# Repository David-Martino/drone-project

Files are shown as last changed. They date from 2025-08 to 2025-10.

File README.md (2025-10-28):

# ELEC5550 3D Mapping and Navigating Autonomous Drone
This is the repository for Team 0-05's final year design project for ELEC5550. The project is to build a drone system capable of autonomously mapping indoor spaces in 3D using onboard sensors, while meeting restrictive power and cost constraints (a 2S 800mAh battery and a $500 budget). Navigation is done using ROS2, running on a ground station connected to the drone over Wi-Fi. Mapping is also done on ROS2, based on UZ-SLAMLab's implementation of ORB-SLAM3 for Visual SLAM and Kimberly McGuire's crazyflie_ros2_multiranger repository for the ToF mapping. The flight controller is based on Espressif's ESP-Drone library, which itself is based on Bitcraze's Crazyflie flight kernel.

<center>

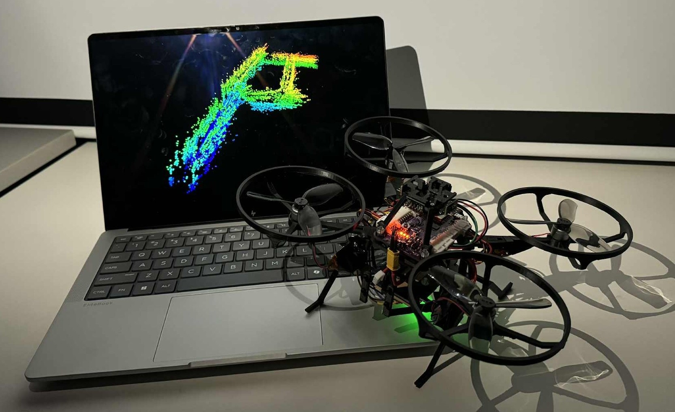
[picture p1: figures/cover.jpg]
Cover


</center>

# Key features 
- Visual SLAM 3D mapping using a monocular Raspberry Pi Camera 3
- Navigation and mapping using an omnidirectional VL53L1 ToF lidar array
- Onboard obstacle avoidance
- Automatic emergency landing procedure for communication loss or critically low battery events.
- Integration with ROS with the option for manual control

# Requirement Verification Evidence
### Test VSM-02: ORB-SLAM3 and Lidar Map
The maps are exported as OctoMap files (.bt). Examples can be found under the `Examples` folder.

ORB-SLAM3             |  ToF Array
:-------------------------:|:-------------------------:
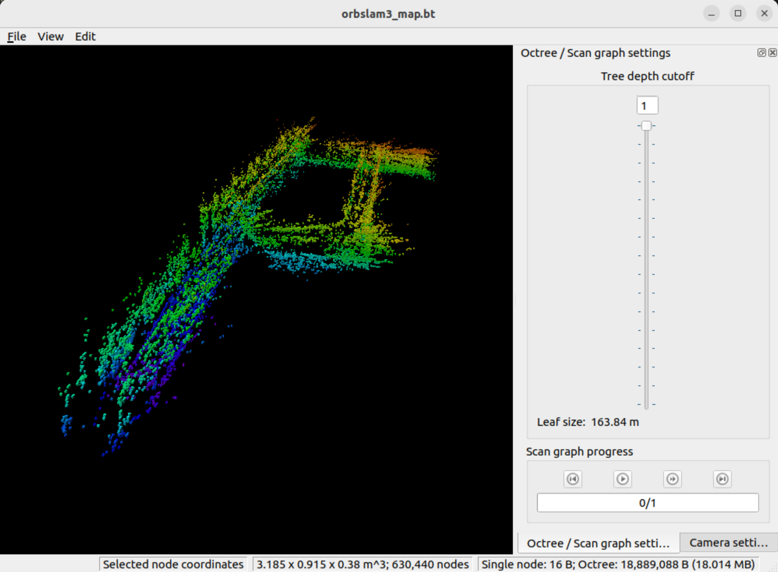
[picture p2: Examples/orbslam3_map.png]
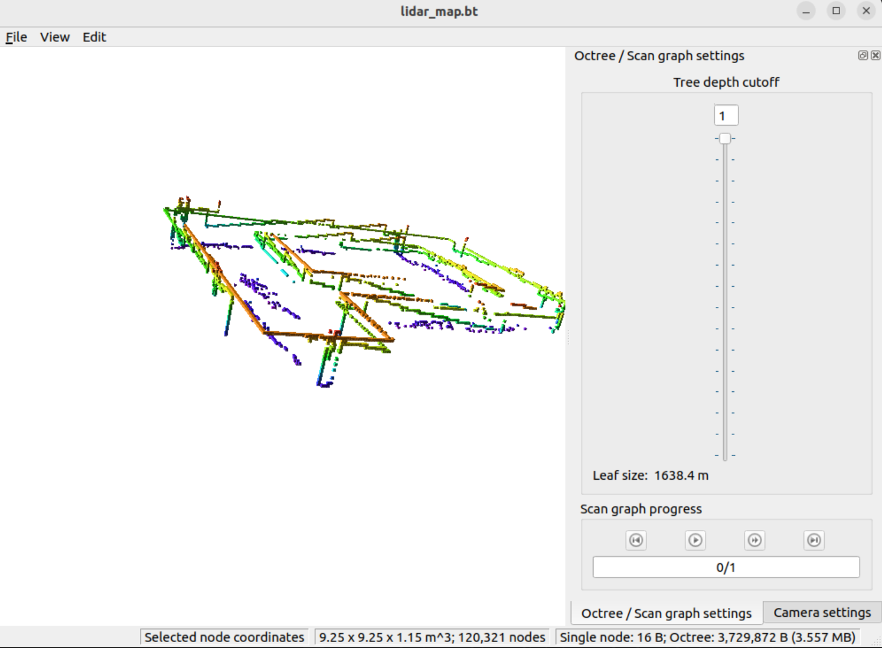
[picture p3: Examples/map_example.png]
  |  

### Test LDR-02: Real-time mapping using the ToF array

<center>

LDR-02 Verfication

</center>

### Test FC-04: Obstacle Avoidance
<center>

FC-04 Verfication

</center>

### Test FC-05: Communication Loss Emergency Landing
The critical battery event follows the same landing procedure, triggering 5 seconds after the event is detected.
<center>

FC-05 Verfication

</center>

# Issues
- Cheap 1104 BLDC motors overheating after ~40 seconds of flight time.
- Significant positional drift while publishing velocity commands.
- ORB-SLAM3 map is not scaled correctly.
- Optical Flow Deck could not be manufactured easily. A VL53L1 breakout board and a PMW3901 breakout board were used for the demonstration.

# Future Work
- Upgrading the FC MCU from an ESP32-S3 to an ESP32-P4. This MCU has hardware H.264 encoding, allowing us to remove the Raspberry Pi and hence vastly reduce the size and weight of the platform.
- Upgrading from visual SLAM to a visual-inertial SLAM using the IMU data for improved map accuracy.
- Changing frame to a more stiff carbon frame (the 3D printed ABS frame is quite flexible, although its unclear if the stability is actually affected by this)
- Custom BLDC ESCs mounted in a more secure location
- Frontier exploration scheme to deterministically map an entire space.
- Improve manufacturability of Optical Flow Deck by extending the pads of the PMW3901 and VL53L1 sensors out from beneath of the component.

# Licence
- Firmware: The firmware folder content is licensed under LGPL-3.0

- Software: The software folder content is released under GPLv3. The dependencies in this workspace are listed below. For a full list of the dependency's licenses, refer to their documentation.
    - ORB-SLAM3 (released under GPLv3)
    - Kimberley McGuire's lidar mapping project (released under the MIT License)

- Hardware: The hardware folder content is licensed under CC-BY-NC-SA 4.0

- Frame: The frame content is licensed under CC-BY-NC-SA 4.0

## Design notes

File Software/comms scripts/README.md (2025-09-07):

# Erwin's Attempt at Implementing David's Scripts

1. Install `Raspberry Pi Imager` on Windows (Ubuntu dual boot wasn't seeing the SD card).
1. Plug in micro SD card (in standard SD card adapter) with write lock off (if present).
1. Choose Device as `Raspberry Pi Zero 2 W`.
1. Choose OS as `Raspberry Pi OS Lite (64-bit)` under Raspberry Pi OS (Other).
1. Choose Storage as the micro SD card you plugged in.
1. Click Next and configure OS settings:
    1. Set username and password (`erwin`, `12345678`).
    1. Configure wireless LAN (`iPhone98`, `12345678`, `AU`).
    1. Set locale settings (`Australia/Perth`, `au`).
    1. Enable SSH (select `Use password authentification`).
1. Continue to flash the SD card.
1. On iPhone hotspot, turn on `Allow Others to Join` and `Maximise Compatibility` to force 2.4GHz wifi.
1. Plug micro SD card into Pi Zero 2 W and start up, with keyboard and monitor connected.
1. Once booted, log in with username and password. 
1. Wait a minute and check if connected to the hotspot with `nmcli device status` and `hostname -I`.
1. If not connected, configure wifi settings with:
    1. Confirm hotspot is visible with `nmcli dev wifi list`.
    1. Connect to hotspot with `sudo nmcli dev wifi connect "iPhone98" password "12345678" ifname wlan0`.
    1. Check connection is in list of saved connections with `nmcli con show`.
    1. Configure autoconnection with `sudo nmcli con mod "iPhone98" connection.autoconnect yes`.
    1. Reboot with `sudo reboot`.
    1. Wait a minute and check if connected to the hotspot with `nmcli device status` and `hostname -I`.
1. Connect to the hotspot with your groundstation.
1. Test SSH connection from your groundstation with `ssh erwin@raspberrypi.local` and `12345678`. 
1. Open a terminal on the groundstation, navigate to `drone-project\comms script\Beacon\`, and run `python .\gs_beacon.py`.
1. Install GStreamer from `https://gstreamer.freedesktop.org/download/#windows` (download and run `MSVC 64-bit runtime installer`).
1. Add GStreamer to path (`C:\Program Files\gstreamer\1.0\msvc_x86_64\bin` on Windows).
1. Launch GStreamer with `gst-launch-1.0 -v udpsrc port=5004 caps="application/x-rtp, media=video, encoding-name=H264, payload=96" ! rtph264depay ! h264parse ! avdec_h264 ! videoconvert ! autovideosink sync=false`. 
1. On the Pi (or via SSH), install with the following:
    ```
    sudo apt update
    sudo apt full-upgrade -y
    sudo reboot
    sudo apt -y install gstreamer1.0-tools gstreamer1.0-plugins-base gstreamer1.0-plugins-good gstreamer1.0-plugins-bad gstreamer1.0-plugins-ugly ffmpeg python3-pip rpicam-apps iperf3
    ```
1. On the groundstation, navigate to `drone-project\comms script\` and copy with the following:
    ```
    scp Beacon\discover_gs.py Startup\Pi-Startup-FFmpeg.service_RevC.service Vido_Uplink\ffmpeg_uplink_RevE.bash erwin@raspberrypi.local:/home/erwin/
    ```
1. On the Pi (or via SSH), move and rename files with the following:
    ```
    sudo mv ~/discover_gs.py /usr/local/bin/
    sudo mv ~/ffmpeg_uplink_RevE.bash /usr/local/bin/ffmpeg_uplink.sh
    sudo chmod +x /usr/local/bin/discover_gs.py /usr/local/bin/ffmpeg_uplink.sh
    sudo mv ~/Pi-Startup-FFmpeg.service_RevC.service /etc/systemd/system/pi-uplink.service
    sudo systemctl daemon-reload
    ```
1. On the Pi (or via SSH), use `sudo nano /etc/systemd/system/pi-uplink.service` to edit the User from `piteam05` to `root`, then save (CTRL+O, ENTER) and exit (CTRL+X).
1. Fix Windows line endings with:
    ```
    sudo apt -y install dos2unix
    sudo dos2unix /usr/local/bin/ffmpeg_uplink.sh /usr/local/bin/discover_gs.py /etc/systemd/system/pi-uplink.service
    ```
1. On the Pi (or via SSH), disable the Pi video preview with `sudo sed -i '0,/rpicam-vid /s//rpicam-vid -n /' /usr/local/bin/ffmpeg_uplink.sh`.  
1. On the Pi (or via SSH), set environment variables and launch streaming with `BASE_IP=172.20.10.6 PORT=5004 W=1280 H=720 FPS=30 BITRATE=4000000 GOP=15 ffmpeg_uplink.sh`. End with `CTRL+C`.
1. On the Pi (or via SSH), change the uplink service details with `sudo nano /etc/systemd/system/pi-uplink.service` to match the following:
    ```
    [Unit]
    Description=Pi Camera → RTP/UDP uplink (beacon + IP fallback)
    After=network-online.target
    Wants=network-online.target

    [Service]
    Type=simple
    User=root
    Group=video
    # Discovery config:
    Environment=BEACON_PORT=9000
    Environment=DISCOVERY_TIMEOUT=20
    Environment=SERVICE_NAME=GS-H264
    # Final fallback:
    Environment=BASE_IP=172.20.10.6
    # Video params:
    Environment=PORT=5004
    Environment=W=1280
    Environment=H=720
    Environment=FPS=30
    Environment=BITRATE=4000000
    Environment=GOP=15
    ExecStartPre=/bin/sleep 3
    ExecStart=/usr/local/bin/ffmpeg_uplink.sh
    Restart=always
    RestartSec=2

    [Install]
    WantedBy=multi-user.target
    ```
1. On the Pi (or via SSH), test the service with:
    ```
    sudo systemctl daemon-reload
    sudo systemctl start pi-uplink.service
    journalctl -u pi-uplink.service -n 20 --no-pager
    ```
1. On the Pi (or via SSH), stop the service and enable autostart with:
    ```
    sudo systemctl stop pi-uplink.service
    sudo systemctl enable --now pi-uplink.service
    ```
1. On the Linux groundstation, install with:
    ```
    sudo apt update && sudo apt -y install \
    gstreamer1.0-tools \
    gstreamer1.0-plugins-base \
    gstreamer1.0-plugins-good \
    gstreamer1.0-plugins-bad \
    gstreamer1.0-plugins-ugly \
    gstreamer1.0-libav \
    ffmpeg \
    python3 \
    python3-pip \
    iperf3
    ```
1. On the Linux groundstation, mnually test receiving the video stream with:
    ```
    gst-launch-1.0 -v udpsrc port=5004 \
    caps="application/x-rtp, media=video, encoding-name=H264, payload=96" \
    ! rtpjitterbuffer latency=60 \
    ! rtph264depay ! h264parse ! avdec_h264 ! videoconvert ! autovideosink sync=false
    ```

To start streaming:
1. Turn on hotspot with `Maximise Compatibility` on.
1. Connect to hotspot from groundstation.
1. CD to `drone-project` directory in terminal and run `make stream`.
1. Power up the Raspberry Pi Zero 2 W, and streaming should start within 30 seconds.

Run `make stop` to end streaming and beaconing on the groundstation.

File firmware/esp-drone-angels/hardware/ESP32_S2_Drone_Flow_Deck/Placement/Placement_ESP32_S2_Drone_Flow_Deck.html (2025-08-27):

D:\newFiles\e32336_esp32s2DroneShield\02_PCB\PCB_200616.pcb Create in 2020/6/16 20:44:25 Total components = 51 component(s)

Component Report
NO. | RefDes | PartDecal | Pins | Layer | Orient | PositionX | PositionY | IsSMD
1 | 1C1 | C0603 | 2 | Top | 180 | 13.100 | 38.379 | Yes
2 | 1C2 | C0402 | 2 | Top | 180 | 13.350 | 37.129 | Yes
3 | 1C3 | C0603 | 2 | Top | 180 | 13.050 | 35.879 | Yes
4 | 1C4 | C0402 | 2 | Top | 180 | 13.350 | 34.679 | Yes
5 | 1C5 | C0603 | 2 | Top | 180 | 13.100 | 32.629 | Yes
6 | 1C6 | C0402 | 2 | Top | 180 | 13.350 | 33.779 | Yes
7 | 1C7 | C0603 | 2 | Top | 0 | 13.100 | 45.879 | Yes
8 | 1C8 | C0603 | 2 | Top | 0 | 13.100 | 39.879 | Yes
9 | 1C9 | C0603 | 2 | Top | 0 | 18.300 | 46.979 | Yes
10 | 1C10 | C0402 | 2 | Top | 270 | 20.800 | 43.479 | Yes
11 | 1C11 | C0402 | 2 | Top | 0 | 18.050 | 45.729 | Yes
12 | 1J1 | CON8-S-2P0 | 16 | Bottom | 90 | 27.800 | 39.629 | No
13 | 1J2 | CON8-S-2P0 | 16 | Bottom | 90 | 2.800 | 39.629 | No
14 | 1R1 | R0402 | 2 | Top | 0 | 13.355 | 31.208 | Yes
15 | 1R2 | R0402 | 2 | Top | 180 | 7.300 | 32.629 | Yes
16 | 1R3 | R0402 | 2 | Top | 180 | 7.300 | 36.629 | Yes
17 | 1R4 | R0402 | 2 | Top | 180 | 7.300 | 38.629 | Yes
18 | 1R5 | R0402 | 2 | Top | 90 | 20.800 | 41.279 | Yes
19 | 1U1 | COB28_0P65_6X6 | 29 | Top | 0 | 18.300 | 34.629 | Yes
20 | 1U2 | SOT-23-5 | 5 | Top | 270 | 12.850 | 42.879 | Yes
21 | 1U3 | LGA12_0P8_2P5X4P9 | 12 | Top | 0 | 18.300 | 42.479 | Yes
22 | 2C1 | C0402 | 2 | Top | 180 | 8.050 | 12.016 | Yes
23 | 2C2 | C0402 | 2 | Top | 180 | 8.050 | 11.016 | Yes
24 | 2C3 | C0402 | 2 | Top | 90 | 11.800 | 14.766 | Yes
25 | 2C4 | C0402 | 2 | Top | 270 | 14.400 | 11.200 | Yes
26 | 2C5 | C0402 | 2 | Top | 270 | 13.400 | 11.200 | Yes
27 | 2C6 | C0402 | 2 | Top | 270 | 16.800 | 11.766 | Yes
28 | 2J1 | CON8-S-2P0 | 16 | Top | 90 | 2.800 | 11.766 | No
29 | 2J2 | CON8-S-2P0 | 16 | Top | 90 | 27.800 | 11.766 | No
30 | 2U1 | LPCC16_0P5_3X3 | 16 | Top | 0 | 11.050 | 11.766 | Yes
31 | 2U2 | QFN8_1P25_3X5 | 8 | Top | 0 | 19.550 | 11.766 | Yes
32 | T1 | HOLE_0P6 | 1 | Top | 0 | 7.000 | 27.864 | No
33 | T2 | HOLE_0P6 | 1 | Top | 0 | 7.900 | 27.864 | No
34 | T3 | HOLE_0P6 | 1 | Top | 0 | 8.800 | 27.864 | No
35 | T4 | HOLE_0P6 | 1 | Top | 0 | 9.700 | 27.864 | No
36 | T5 | HOLE_0P6 | 1 | Top | 0 | 10.600 | 27.864 | No
37 | T6 | HOLE_0P6 | 1 | Top | 0 | 10.600 | 23.500 | No
38 | T7 | HOLE_0P6 | 1 | Top | 0 | 9.700 | 23.500 | No
39 | T8 | HOLE_0P6 | 1 | Top | 0 | 8.800 | 23.500 | No
40 | T9 | HOLE_0P6 | 1 | Top | 0 | 7.900 | 23.500 | No
41 | T10 | HOLE_0P6 | 1 | Top | 0 | 7.000 | 23.500 | No
42 | T11 | HOLE_0P6 | 1 | Top | 0 | 19.600 | 27.864 | No
43 | T12 | HOLE_0P6 | 1 | Top | 0 | 20.500 | 27.864 | No
44 | T13 | HOLE_0P6 | 1 | Top | 0 | 21.400 | 27.864 | No
45 | T14 | HOLE_0P6 | 1 | Top | 0 | 22.300 | 27.864 | No
46 | T15 | HOLE_0P6 | 1 | Top | 0 | 23.200 | 27.864 | No
47 | T16 | HOLE_0P6 | 1 | Top | 0 | 19.600 | 23.500 | No
48 | T17 | HOLE_0P6 | 1 | Top | 0 | 20.500 | 23.500 | No
49 | T18 | HOLE_0P6 | 1 | Top | 0 | 21.400 | 23.500 | No
50 | T19 | HOLE_0P6 | 1 | Top | 0 | 22.300 | 23.500 | No
51 | T20 | HOLE_0P6 | 1 | Top | 0 | 23.200 | 23.500 | No

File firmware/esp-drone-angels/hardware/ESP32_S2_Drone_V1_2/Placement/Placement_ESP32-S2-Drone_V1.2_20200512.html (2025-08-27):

D:\WORK\#31436_ESP32-S2-ESPlane-KIT_M_V1.0_N_XX_20200325_V0.1\#31436_ESP32-S2-ESPlane-KIT_M_V1.2_N_XX_20200511_V0.3\02_PCB/PCB_ESP32-S2-Drone_V1.2_20200512.pcb Create in 2020/5/12 17:13:59 Total components = 203 component(s)

Component Report
NO. | RefDes | PartDecal | Pins | Layer | Orient | PositionX | PositionY | IsSMD
1 | C1 | C0603 | 2 | Top | 180 | 1571.554 | 2462.404 | Yes
2 | C2 | C0402 | 2 | Top | 90 | 1685.304 | 2562.104 | Yes
3 | C3 | C0603 | 2 | Top | 180 | 1555.454 | 2230.404 | Yes
4 | C4 | C0402 | 2 | Top | 270 | 1923.504 | 2559.904 | Yes
5 | C5 | C0402 | 2 | Top | 270 | 1771.004 | 2562.104 | Yes
6 | C6 | C0603 | 2 | Top | 0 | 2787.933 | 2016.722 | Yes
7 | C7 | C0402 | 2 | Top | 0 | 2808.406 | 1922.234 | Yes
8 | C8 | C0603 | 2 | Top | 180 | 2671.004 | 2016.722 | Yes
9 | C9 | C0402 | 2 | Top | 90 | 2750.925 | 1943.888 | Yes
10 | C10 | C0603 | 2 | Top | 180 | 1711.454 | 2230.404 | Yes
11 | C11 | C0603 | 2 | Top | 180 | 1706.504 | 2462.404 | Yes
12 | C12 | C0603 | 2 | Top | 180 | 1426.004 | 2117.254 | Yes
13 | C13 | C0402 | 2 | Top | 0 | 2231.004 | 2304.754 | Yes
14 | C14 | C0603 | 2 | Top | 90 | 2369.754 | 2361.004 | Yes
15 | C15 | C0603 | 2 | Top | 90 | 2169.754 | 2403.504 | Yes
16 | C16 | C0603 | 2 | Top | 180 | 2409.843 | 1237.402 | Yes
17 | C17 | C0402 | 2 | Top | 180 | 2398.031 | 1188.189 | Yes
18 | C18 | C0402 | 2 | Top | 270 | 1571.260 | 1214.173 | Yes
19 | C19 | C0402 | 2 | Top | 270 | 1852.254 | 2286.004 | Yes
20 | C20 | C0402 | 2 | Top | 0 | 2028.839 | 2377.254 | Yes
21 | C21 | C0402 | 2 | Top | 90 | 1959.604 | 2393.504 | Yes
22 | C22 | C0402 | 2 | Top | 180 | 1918.504 | 2141.004 | Yes
23 | C23 | C0402 | 2 | Top | 0 | 1139.370 | 1915.354 | Yes
24 | C24 | C0402 | 2 | Top | 0 | 1139.754 | 1604.754 | Yes
25 | D1 | SOD523 | 2 | Top | 315 | 1382.254 | 1399.754 | Yes
26 | D2 | SOD523 | 2 | Top | 45 | 1389.754 | 2547.254 | Yes
27 | D3 | SOD323 | 2 | Top | 90 | 2376.004 | 2237.254 | Yes
28 | D4 | SOD523 | 2 | Top | 135 | 2549.754 | 2552.254 | Yes
29 | D5 | SOD523 | 2 | Top | 0 | 2744.754 | 1419.754 | Yes
30 | D6 | LED3010-S | 3 | Top | 0 | 1476.378 | 2814.961 | Yes
31 | D7 | LED3010-S | 3 | Top | 180 | 1476.378 | 1122.047 | Yes
32 | D8 | LED3010-S | 3 | Top | 0 | 2460.630 | 2814.961 | Yes
33 | D9 | LED3010-S | 3 | Top | 180 | 2460.630 | 1122.047 | Yes
34 | FB1 | L0603 | 2 | Top | 90 | 2409.754 | 1328.504 | Yes
35 | H1 | P_2X1 | 1 | Bottom | 135 | 2814.964 | 2657.484 | Yes
36 | H58 | P_2X1 | 1 | Bottom | 45 | 708.661 | 3346.457 | Yes
37 | H59 | P_2X1 | 1 | Bottom | 45 | 1279.528 | 2814.961 | Yes
38 | H60 | P_2X1 | 1 | Bottom | 45 | 2657.480 | 1122.047 | Yes
39 | H61 | P_2X1 | 1 | Bottom | 45 | 3228.346 | 590.551 | Yes
40 | H62 | P_2X1 | 1 | Bottom | 135 | 1122.047 | 1279.528 | Yes
41 | H63 | P_2X1 | 1 | Bottom | 45 | 1122.047 | 2657.480 | Yes
42 | H65 | P_2X1 | 1 | Bottom | 45 | 3346.457 | 708.661 | Yes
43 | H66 | P_2X1 | 1 | Bottom | 135 | 2657.480 | 2814.961 | Yes
44 | H67 | P_2X1 | 1 | Bottom | 135 | 1279.528 | 1122.047 | Yes
45 | H68 | P_2X1 | 1 | Bottom | 135 | 590.551 | 708.661 | Yes
46 | H69 | P_2X1 | 1 | Bottom | 45 | 590.551 | 3228.346 | Yes
47 | H70 | P_2X1 | 1 | Bottom | 45 | 2814.961 | 1279.528 | Yes
48 | H71 | P_2X1 | 1 | Bottom | 135 | 3346.457 | 3228.346 | Yes
49 | H72 | P_2X1 | 1 | Bottom | 135 | 708.661 | 590.551 | Yes
50 | H73 | P_2X1 | 1 | Bottom | 135 | 3228.346 | 3346.457 | Yes
51 | J1 | USB_5P_MICRO_F | 11 | Top | 180 | 2638.504 | 2303.504 | No
52 | J2 | FFC24-0P5 | 26 | Top | 180 | 1968.504 | 2736.220 | Yes
53 | J3 | A2005HWV-S-XP-A | 16 | Top | 270 | 2460.630 | 1751.969 | No
54 | J4 | A2005HWV-S-XP-A | 16 | Top | 270 | 1476.378 | 1751.969 | No
55 | J5 | CON2X1_1P5_SMT_ZH-2A_DIP | 4 | Top | 45 | 2678.504 | 2678.504 | No
56 | J6 | CON2X1_1P5_SMT_ZH-2A_DIP | 4 | Top | 315 | 2678.504 | 1258.504 | No
57 | J7 | CON2X1_2P0_SMT_PH2A-S-A | 4 | Top | 270 | 1478.346 | 2288.504 | Yes
58 | J8 | CON2X1_1P5_SMT_ZH-2A_DIP | 4 | Top | 225 | 1258.504 | 1258.504 | No
59 | J9 | CON2X1_1P5_SMT_ZH-2A_DIP | 4 | Top | 135 | 1258.504 | 2678.504 | No
60 | J10 | A2005HWV-S-XP-A | 16 | Top | 270 | 1476.378 | 463.219 | No
61 | J11 | A2005HWV-S-XP-A | 16 | Top | 270 | 2460.630 | 463.219 | No
62 | Q3 | SOT-23-3 | 3 | Top | 180 | 1291.334 | 2033.504 | Yes
63 | Q4 | SOT-23-3 | 3 | Top | 0 | 1218.504 | 1512.004 | Yes
64 | Q5 | SOT-23-3 | 3 | Top | 270 | 1518.504 | 2667.254 | Yes
65 | Q6 | SOT-23-3 | 3 | Top | 90 | 2418.504 | 2667.504 | Yes
66 | Q7 | SOT-23-3 | 3 | Top | 0 | 2718.504 | 1512.004 | Yes
67 | R1 | R0402 | 2 | Top | 180 | 2533.504 | 2143.504 | Yes
68 | R3 | R0402 | 2 | Top | 0 | 2454.754 | 2143.504 | Yes
69 | R5 | R0402 | 2 | Top | 90 | 1868.404 | 2559.904 | Yes
70 | R6 | R0402 | 2 | Top | 270 | 1736.904 | 2562.104 | Yes
71 | R7 | R0402 | 2 | Top | 90 | 2709.193 | 1943.888 | Yes
72 | R8 | R0402 | 2 | Top | 0 | 2808.012 | 1963.967 | Yes
73 | R9 | R0402 | 2 | Top | 0 | 2646.201 | 1929.321 | Yes
74 | R10 | R0402 | 2 | Top | 0 | 2646.201 | 1964.754 | Yes
75 | R11 | R0402 | 2 | Top | 90 | 1321.260 | 1581.890 | Yes
76 | R12 | R0402 | 2 | Top | 90 | 1356.693 | 1581.890 | Yes
77 | R13 | R0402 | 2 | Top | 180 | 1232.254 | 1604.754 | Yes
78 | R14 | R0402 | 2 | Top | 180 | 1675.504 | 2619.904 | Yes
79 | R15 | R0402 | 2 | Top | 90 | 2583.996 | 1996.348 | Yes
80 | R16 | R0402 | 2 | Top | 270 | 2583.996 | 1916.148 | Yes
81 | R17 | R0402 | 2 | Top | 0 | 1253.504 | 2123.504 | Yes
82 | R18 | R0402 | 2 | Top | 180 | 2231.004 | 2267.854 | Yes
83 | R19 | R0402 | 2 | Top | 0 | 1139.754 | 1871.004 | Yes
84 | R20 | R0402 | 2 | Top | 90 | 2287.254 | 2288.504 | Yes
85 | R21 | R0402 | 2 | Top | 180 | 1538.976 | 1357.480 | Yes
86 | R22 | R0402 | 2 | Top | 90 | 1536.614 | 1214.173 | Yes
87 | R23 | R0402 | 2 | Top | 180 | 2381.004 | 2563.504 | Yes
88 | R24 | R0402 | 2 | Top | 90 | 2622.254 | 1529.754 | Yes
89 | R25 | R0402 | 2 | Top | 180 | 1538.976 | 1397.638 | Yes
90 | R26 | R0402 | 2 | Top | 180 | 1516.004 | 2763.504 | Yes
91 | R27 | R0402 | 2 | Top | 0 | 2018.604 | 2121.004 | Yes
92 | R28 | R0402 | 2 | Top | 0 | 1887.254 | 2377.254 | Yes
93 | R29 | R0402 | 2 | Top | 90 | 1448.504 | 1214.754 | Yes
94 | R30 | R0402 | 2 | Top | 180 | 2499.754 | 2763.504 | Yes
95 | R31 | R0402 | 2 | Top | 0 | 2476.772 | 1188.189 | Yes
96 | R32 | R0402 | 2 | Top | 270 | 2086.004 | 2360.504 | Yes
97 | R33 | R0402 | 2 | Top | 90 | 2086.004 | 2280.504 | Yes
98 | R34 | R0402 | 2 | Top | 0 | 1282.254 | 1759.754 | Yes
99 | R35 | R0402 | 2 | Top | 90 | 1344.754 | 1702.254 | Yes
100 | SW1 | SW4_3X3P5X1P1_SMT | 6 | Top | 270 | 1141.704 | 2047.244 | No
101 | SW2 | SW4_3X3P5X1P1_SMT | 6 | Top | 270 | 1141.732 | 1740.157 | No
102 | T1 | K_3X2 | 1 | Top | 0 | 68.504 | 2242.504 | No
103 | T2 | K_3X2 | 1 | Top | 0 | 68.504 | 2095.504 | No
104 | T3 | K_3X2 | 1 | Top | 0 | 720.472 | 2242.504 | No
105 | T4 | K_3X2 | 1 | Top | 0 | 720.472 | 2095.504 | No
106 | T5 | K_3X2 | 1 | Top | 0 | 68.504 | 1841.504 | No
107 | T6 | K_3X2 | 1 | Top | 0 | 68.504 | 1694.504 | No
108 | T7 | K_3X2 | 1 | Top | 0 | 720.474 | 1841.504 | No
109 | T8 | K_3X2 | 1 | Top | 0 | 720.472 | 1694.504 | No
110 | T9 | K_3X2 | 1 | Top | 180 | 1648.504 | 3512.254 | No
111 | T10 | K_3X2 | 1 | Top | 180 | 1648.504 | 3366.004 | No
112 | T11 | K_3X2 | 1 | Top | 180 | 3868.504 | 2242.504 | No
113 | T12 | K_3X2 | 1 | Top | 180 | 3868.504 | 2094.754 | No
114 | T13 | K_3X2 | 1 | Top | 180 | 2276.504 | 3512.254 | No
115 | T14 | K_3X2 | 1 | Top | 180 | 2276.504 | 3366.004 | No
116 | T15 | K_3X2 | 1 | Top | 180 | 3868.504 | 1841.504 | No
117 | T16 | K_3X2 | 1 | Top | 180 | 3868.504 | 1694.754 | No
118 | T17 | K_3X2 | 1 | Top | 0 | 3216.504 | 2242.504 | No
119 | T18 | K_3X2 | 1 | Top | 0 | 3216.504 | 2095.504 | No
120 | T19 | K_3X2 | 1 | Top | 0 | 3216.504 | 1841.504 | No
121 | T20 | K_3X2 | 1 | Top | 0 | 3216.504 | 1694.504 | No
122 | T21 | SMD_3X6 | 1 | Top | 225 | 3359.055 | 495.669 | No
123 | T22 | HOLE_0P6 | 1 | Top | 0 | 717.649 | 2527.559 | No
124 | T23 | SMD_3X6 | 1 | Top | 45 | 3881.102 | 136.220 | No
125 | T24 | SMD_3X6 | 1 | Top | 135 | 3813.386 | 3888.583 | No
126 | T25 | SMD_3X6 | 1 | Top | 315 | 3446.063 | 3375.591 | No
127 | T26 | SMD_3X6 | 1 | Top | 225 | 47.638 | 3812.205 | No
128 | T27 | SMD_3X6 | 1 | Top | 45 | 585.039 | 3433.071 | No
129 | T28 | SMD_3X6 | 1 | Top | 135 | 497.638 | 582.677 | No
130 | T29 | SMD_3X6 | 1 | Top | 315 | 124.409 | 45.669 | No
131 | T30 | HOLE_0P6 | 1 | Top | 0 | 717.649 | 2500.000 | No
132 | T31 | HOLE_0P6 | 1 | Top | 0 | 717.649 | 2472.441 | No
133 | T32 | HOLE_0P6 | 1 | Top | 0 | 717.649 | 2417.323 | No
134 | T33 | HOLE_0P6 | 1 | Top | 0 | 717.649 | 1519.685 | No
135 | T34 | HOLE_0P6 | 1 | Top | 0 | 717.649 | 1492.126 | No
136 | T35 | HOLE_0P6 | 1 | Top | 0 | 717.649 | 1464.567 | No
137 | T36 | HOLE_0P6 | 1 | Top | 0 | 717.649 | 1409.449 | No
138 | T37 | HOLE_0P6 | 1 | Top | 0 | 717.649 | 1437.008 | No
139 | T38 | HOLE_0P6 | 1 | Top | 0 | 1076.772 | 1519.685 | No
140 | T39 | HOLE_0P6 | 1 | Top | 0 | 1076.772 | 1492.126 | No
141 | T40 | HOLE_0P6 | 1 | Top | 0 | 1076.772 | 1464.567 | No
142 | T41 | HOLE_0P6 | 1 | Top | 0 | 1076.772 | 1409.449 | No
143 | T42 | HOLE_0P6 | 1 | Top | 0 | 1076.772 | 1437.008 | No
144 | T43 | HOLE_0P6 | 1 | Top | 0 | 1076.772 | 2531.496 | No
145 | T44 | HOLE_0P6 | 1 | Top | 0 | 1076.772 | 2503.937 | No
146 | T45 | HOLE_0P6 | 1 | Top | 0 | 1076.772 | 2476.378 | No
147 | T46 | HOLE_0P6 | 1 | Top | 0 | 1076.772 | 2448.819 | No
148 | T47 | HOLE_0P6 | 1 | Top | 0 | 1076.772 | 2421.260 | No
149 | T48 | HOLE_0P6 | 1 | Top | 0 | 3219.359 | 2531.496 | No
150 | T49 | HOLE_0P6 | 1 | Top | 0 | 3219.359 | 2503.937 | No
151 | T50 | HOLE_0P6 | 1 | Top | 0 | 3219.359 | 2476.378 | No
152 | T51 | HOLE_0P6 | 1 | Top | 0 | 3219.359 | 2448.819 | No
153 | T52 | HOLE_0P6 | 1 | Top | 0 | 3219.359 | 2421.260 | No
154 | T53 | HOLE_0P6 | 1 | Top | 0 | 3219.359 | 1515.748 | No
155 | T54 | HOLE_0P6 | 1 | Top | 0 | 3219.359 | 1488.189 | No
156 | T55 | HOLE_0P6 | 1 | Top | 0 | 3219.359 | 1460.630 | No
157 | T56 | HOLE_0P6 | 1 | Top | 0 | 3219.359 | 1433.071 | No
158 | T57 | HOLE_0P6 | 1 | Top | 0 | 3219.359 | 1405.512 | No
159 | T58 | HOLE_0P6 | 1 | Top | 0 | 717.649 | 2444.882 | No
160 | T59 | HOLE_0P6 | 1 | Top | 0 | 2860.236 | 1519.685 | No
161 | T60 | HOLE_0P6 | 1 | Top | 0 | 2860.236 | 1492.126 | No
162 | T61 | HOLE_0P6 | 1 | Top | 0 | 2860.236 | 1464.567 | No
163 | T62 | HOLE_0P6 | 1 | Top | 0 | 2860.236 | 1437.008 | No
164 | T63 | HOLE_0P6 | 1 | Top | 0 | 2860.236 | 1409.449 | No
165 | T64 | HOLE_0P6 | 1 | Top | 0 | 2860.236 | 2531.496 | No
166 | T65 | HOLE_0P6 | 1 | Top | 0 | 2860.236 | 2503.937 | No
167 | T66 | HOLE_0P6 | 1 | Top | 0 | 2860.236 | 2476.378 | No
168 | T67 | HOLE_0P6 | 1 | Top | 0 | 2860.236 | 2448.819 | No
169 | T68 | HOLE_0P6 | 1 | Top | 0 | 2860.236 | 2421.260 | No
170 | T69 | HOLE_0P6 | 1 | Top | 0 | 1549.291 | 1074.803 | No
171 | T70 | HOLE_0P6 | 1 | Top | 0 | 1576.850 | 1074.803 | No
172 | T71 | HOLE_0P6 | 1 | Top | 0 | 1604.409 | 1074.803 | No
173 | T72 | HOLE_0P6 | 1 | Top | 0 | 1631.969 | 1074.803 | No
174 | T73 | HOLE_0P6 | 1 | Top | 0 | 1549.291 | 925.197 | No
175 | T74 | HOLE_0P6 | 1 | Top | 0 | 1576.850 | 925.197 | No
176 | T75 | HOLE_0P6 | 1 | Top | 0 | 1604.409 | 925.197 | No
177 | T76 | HOLE_0P6 | 1 | Top | 0 | 1631.969 | 925.197 | No
178 | T77 | HOLE_0P6 | 1 | Top | 0 | 2305.315 | 925.197 | No
179 | T78 | HOLE_0P6 | 1 | Top | 0 | 2332.874 | 925.197 | No
180 | T79 | HOLE_0P6 | 1 | Top | 0 | 2360.433 | 925.197 | No
181 | T80 | HOLE_0P6 | 1 | Top | 0 | 2387.992 | 925.197 | No
182 | T81 | HOLE_0P6 | 1 | Top | 0 | 2305.315 | 1074.803 | No
183 | T82 | HOLE_0P6 | 1 | Top | 0 | 2332.874 | 1074.803 | No
184 | T83 | HOLE_0P6 | 1 | Top | 0 | 2360.433 | 1074.803 | No
185 | T84 | HOLE_0P6 | 1 | Top | 0 | 2387.992 | 1074.803 | No
186 | T85 | HOLE_0P6 | 1 | Top | 0 | 1913.386 | 3464.567 | No
187 | T86 | HOLE_0P6 | 1 | Top | 0 | 1940.945 | 3464.567 | No
188 | T87 | HOLE_0P6 | 1 | Top | 0 | 1968.504 | 3464.567 | No
189 | T88 | HOLE_0P6 | 1 | Top | 0 | 1996.063 | 3464.567 | No
190 | T89 | HOLE_0P6 | 1 | Top | 0 | 2023.622 | 3464.567 | No
191 | T91 | HOLE_0P6 | 1 | Top | 0 | 1913.386 | 2862.205 | No
192 | T92 | HOLE_0P6 | 1 | Top | 0 | 1940.945 | 2862.205 | No
193 | T93 | HOLE_0P6 | 1 | Top | 0 | 1968.504 | 2862.205 | No
194 | T94 | HOLE_0P6 | 1 | Top | 0 | 1996.063 | 2862.205 | No
195 | T95 | HOLE_0P6 | 1 | Top | 0 | 2023.622 | 2862.205 | No
196 | U1 | SOT23-6 | 6 | Top | 270 | 2493.504 | 2253.504 | Yes
197 | U2 | SOT-23-5 | 5 | Top | 90 | 1500.354 | 2313.104 | Yes
198 | U3 | QFN28_0P5_5 | 29 | Top | 180 | 2688.720 | 1776.959 | Yes
199 | U4 | SOT-23-5 | 5 | Top | 90 | 1656.354 | 2313.104 | Yes
200 | U5 | DFN3030-8 | 9 | Top | 270 | 2264.754 | 2392.254 | Yes
201 | U6 | ESP32-S2-WROVER | 43 | Top | 180 | 2322.835 | 834.646 | Yes
202 | U7 | QFN24_0P5_4_A | 24 | Top | 180 | 1968.504 | 2256.204 | Yes
203 | U8 | SOT363 | 6 | Top | 90 | 1284.754 | 1689.754 | Yes

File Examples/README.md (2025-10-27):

# Viewing the Saved OctoMap (`map.bt`)

This repository includes a pre-generated **OctoMap** file (`map.bt`) that represents a 3D occupancy grid built using ROS 2 and OctoMap Server.

##  Quick Instructions (for Ubuntu + ROS 2 Humble)

1. **Install the OctoMap visualisation tool:**
   ```bash
   sudo apt update
   sudo apt install ros-humble-octovis
   ```

2. **Open the map file:**
   ```bash
   octovis map.bt
   ```

This will launch the **OctoMap Viewer (OctoVis)** GUI, allowing you to explore the 3D voxel map interactively — you can zoom, rotate, and toggle occupied/free voxels.

---

## Notes

- The file `map.bt` must be in your current working directory when running the command, or you can specify its full path, e.g.:
  ```bash
  octovis /path/to/map.bt
  ```

---

## Preview

OctoMap preview

OctoMap preview

---

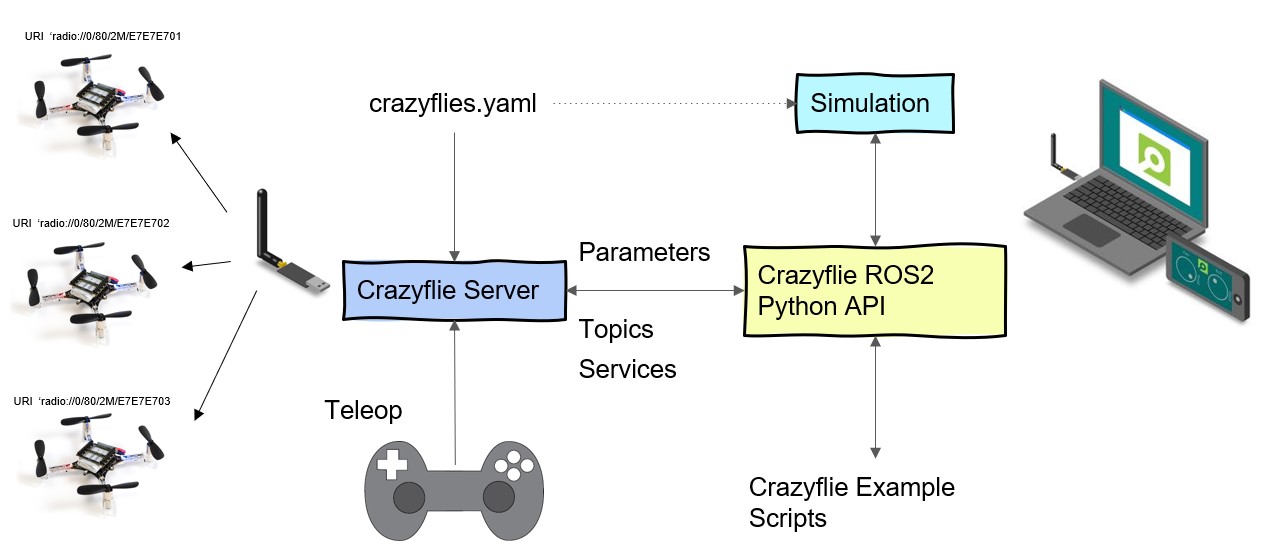
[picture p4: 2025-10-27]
Software/GSC/MRD workspace/crazyflie_mapping_demo/ros2_ws/src/crazyswarm2/docs2/images/overview_nodes.jpg

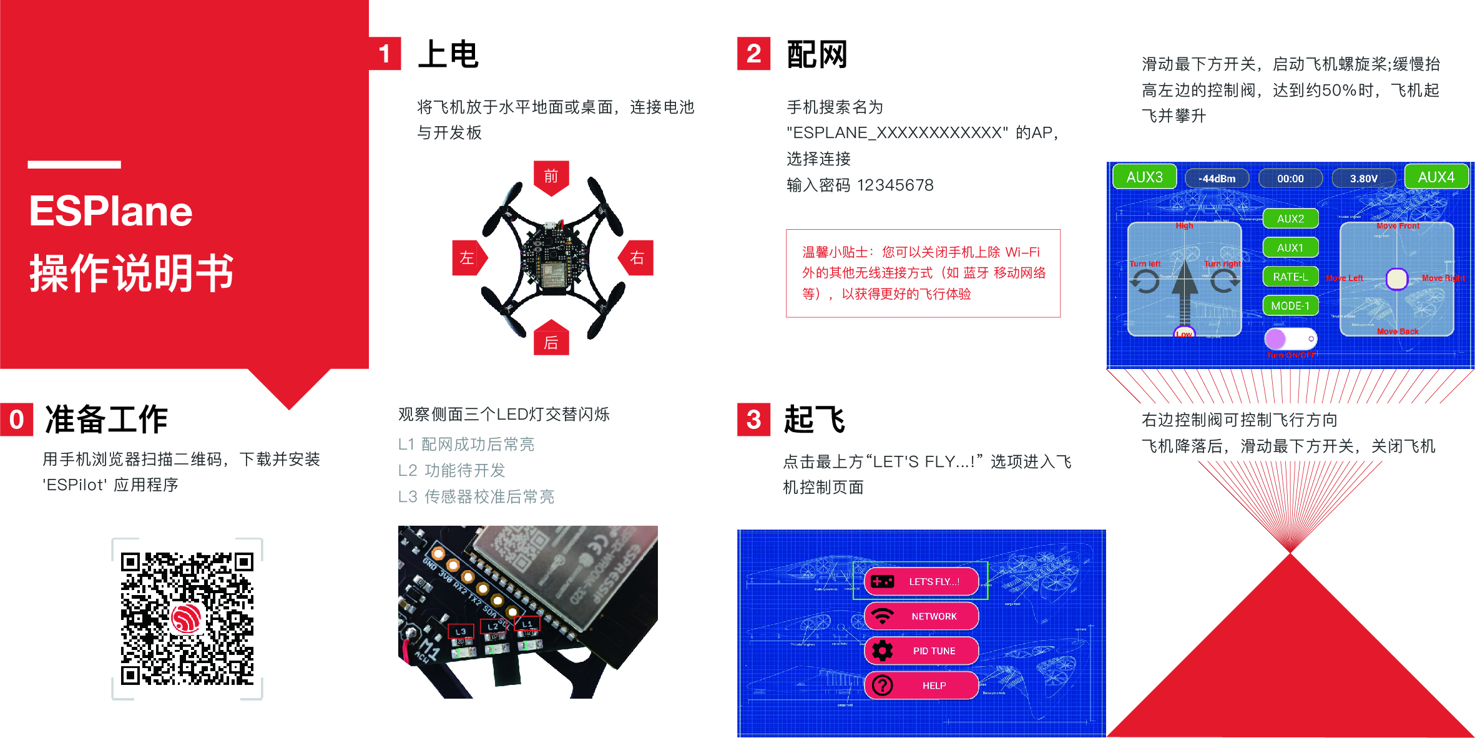
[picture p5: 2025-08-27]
firmware/esp-drone-angels/docs/_static/esplane_v1_specification.jpg

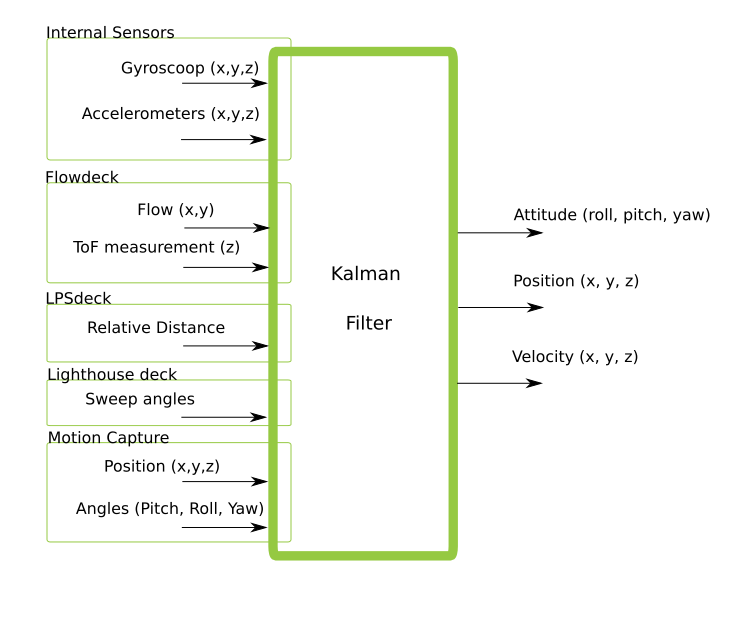
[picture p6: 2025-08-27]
firmware/esp-drone-angels/docs/_static/Schematic-overview-of-inputs-and-outputs-of-the-Extended-Kalman-Filter.png

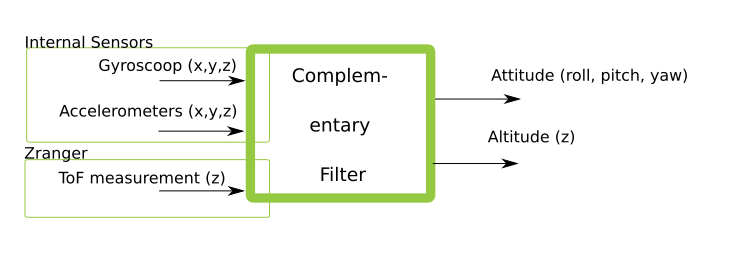
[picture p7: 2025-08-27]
firmware/esp-drone-angels/docs/_static/Schematic-overview-of-inputs-and-outputs-of-the-Complementary-filter.png

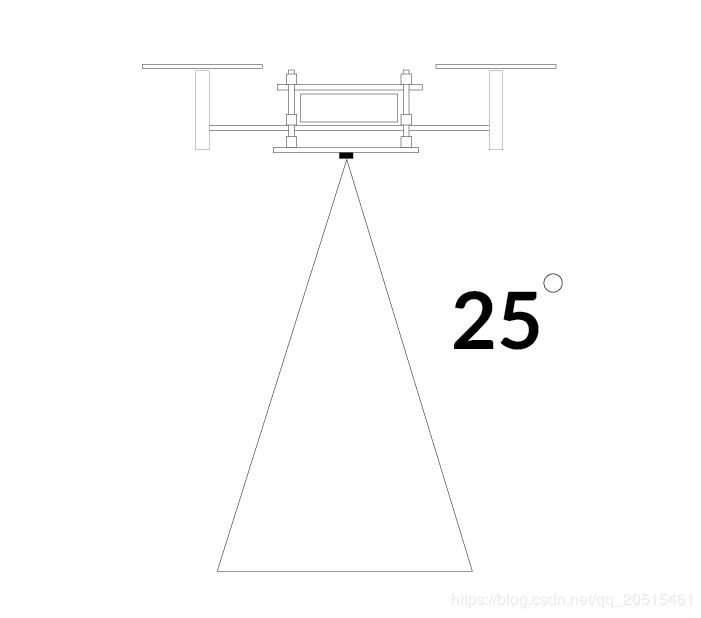
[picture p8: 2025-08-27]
firmware/esp-drone-angels/docs/_static/vl53lxx_roi_2.png

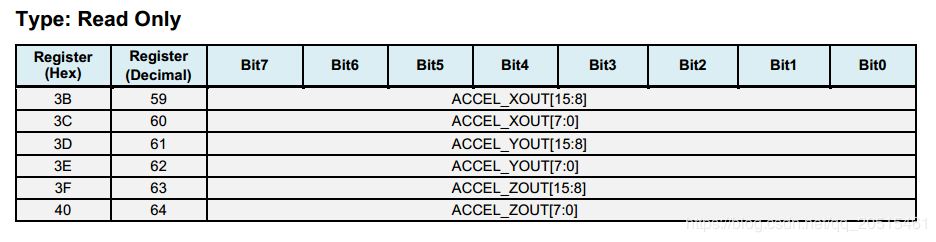
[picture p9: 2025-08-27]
firmware/esp-drone-angels/docs/_static/REG_3B_40.png

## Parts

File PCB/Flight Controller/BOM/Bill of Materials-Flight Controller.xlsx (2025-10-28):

Comment | Description | Designator | Footprint | LibRef | Quantity
5003 | Test Point, Orange, Height 4.6 mm, Tail Length 3 mm, 1-Pin THD, RoHS | +3V3, +5V, GND, V_PROT | KSTN-5003 | CMP-002-00037-2 | 4
CC0603KRX7R9BB104 | Ceramic Capacitor, Multilayer, Ceramic, 50V, 10% +Tol, 10% -Tol, X7R, 15% TC, 0.1uF, Surface Mount, 0603 | C1, C5, C6, C7, C11, C12, C28, C29, C32 | FP-CC0603-DA-IPC_B | CMP-001-00087-1 | 9
CL10A475KP8NNNC | Ceramic Capacitor, Multilayer, Ceramic, 10V, 10% +Tol, 10% -Tol, X5R, 15% TC, 4.7uF, Surface Mount, 0603 | C3, C9, C27, C31 | FP-CL10-IPC_B | CMP-001-00089-1 | 4
CC0603KRX7R8BB105 | Ceramic Capacitor, Multilayer, Ceramic, 25V, 10% +Tol, 10% -Tol, X7R, 15% TC, 1uF, Surface Mount, 0603 | C4 | FP-CC0603-DA-IPC_B | CMP-001-00086-1 | 1
CL31A226KAHNNNE | Ceramic Capacitor, Multilayer, Ceramic, 25V, 10% +Tol, 10% -Tol, X5R, 15% TC, 22uF, Surface Mount, 1206 | C13, C14, C15, C16, C17 | CAPC320160X160_CL31H-0_2_M | CMP-001-00083-2 | 5
GRM188R61C106KAALD | Ceramic Capacitor, Multilayer, Ceramic, 16V, 10% +Tol, 10% -Tol, X5R, 15% TC, 10uF, Surface Mount, 0603 | C18, C19, C20, C21, C33 | FP-GRM18-0_15-IPC_B | CMP-001-00084-1 | 5
CC0603KRX7R9BB222 | Ceramic Capacitor, Multilayer, Ceramic, 50V, 10% +Tol, 10% -Tol, X7R, 15% TC, 0.0022uF, Surface Mount, 0603 | C30 | FP-CC0603-DA-IPC_B | CMP-001-00088-1 | 1
B360A-13-F | Rectifier Diode, Schottky, 1 Phase, 1 Element, 3A, 60V V(RRM), Silicon | D5 | FP-SMA-MFG | CMP-004-00031-1 | 1
RT0603BRD07-2K7L | Fixed Resistor, Thin Film, 0.1W, 2700ohm, 75V, 0.1% +/-Tol, 25ppm/Cel, Surface Mount, 0603 | DNP2, DNP3, R41, R42, R44 | FP-RT0603-IPC_C | CMP-009-00190-1 | 5
HSMS-C190 | Single Color LED, High Efficiency Red, Untinted Diffused, 1mm | DS1 | AVAG-HSMX-C190_V | CMP-007-00037-1 | 1
HSMG-C190 | Single Color LED, Green, Untinted Diffused, 1mm | DS2 | AVAG-HSMX-C190_V | CMP-007-00039-1 | 1
HSMR-C190 | LED Uni-Color Blue, 78 mW, 20 mA, -40 to 85 degC, 2-Pin SMD, RoHS, Tape and Reel | DS3 | AVAG-HSMX-C190_V | CMP-007-00015-2 | 1
HSMD-C170 | Single Color LED, Orange, Untinted Diffused, 1.4mm | DS4, DS6, DS7 | AVAG-HSMX-C170_V | CMP-007-00036-1 | 3
3413.0330.22 | Electric Fuse, Time Lag Blow, 15A, 32VAC, 63VDC, 100A (IR), Surface Mount, 1206 | F1 | FP-3413_0330_22-MFG | CMP-005-00015-1 | 1
S8B-XH-A(LF)(SN) | Conn Shrouded Header (4 Sides) HDR 8 POS 2.5mm Solder RA Thru-Hole Box | FLOW_DECK | FP-S8B-XH-A_LF_SN-MFG | CMP-002-00074-1 | 1
ESP32-S3-WROOM-1-N16R8 | Multiprotocol Modules SMD Module | IC1 | ESP32S3WROOM1N16R8 | CMP-031-00009-1 | 1
AP2114H-3.3TRG1 | 1A 3.3V Low Noise LDO Regulator SOT223 DiodesZetex AP2114H-3.3TRG1 | IC2 | SOT230P700X180-4N | CMP-031-00007-1 | 1
MMC5983MA | 3-AXIS MAGNETIC SENSOR | IC3 | MMC5983MA | CMP-031-00008-2 | 1
TSW-102-07-G-S | CONN HEADER VERT 2POS 2.54MM | LEFT_MOT, RIGHT_MOT | FP-TSW-102-07-G-S-MFG | CMP-02766-000084-1 | 2
S4B-XH-A(LF)(SN) | Male Header, Pitch 2.5 mm, 1 x 4 Position, Height 6.1 mm, Tail Length 3.4 mm, -25 to 85 degC, RoHS, Bulk | MOT1, MOT2, MOT3, MOT4, RANGER_DECK, RPI_ZERO | JST-S4B-XH-A(LF)(SN)_V | CMP-002-00034-2 | 6
150060RS75000 | Single Color LED, Red, Water Clear, 1.1mm | PORT | WL-SMCW_0603_150060xx75000 | CMP-007-00044-1 | 1
XT30PW-F | Socket; DC supply; XT30; female; PIN:2; on PCBs; THT; Colour: yellow | PWR_IN | XT30PWF | CMP-002-00080-2 | 1
450404015514 | Slide Switch | PWR_SW | 450404015514 | CMP-011-00014-1 | 1
SI4204DY-T1-GE3 | Dual N-Ch MOSFET SO-8 BWL 20V 4.6mohm @ | Q1 | SOIC127P600X175-8N | CMP-008-000002-1 | 1
SI5419DU-T1-GE3 | Vishay SI5419DU-T1-GE3 P-channel MOSFET Transistor | Q2 | SI5419DUT1GE3 | CMP-008-000001-1 | 1
BC847BDW1T1G | Small Signal Bipolar Transistor, 0.1A I(C), 45V V(BR)CEO, 2-Element, NPN, Silicon | Q6 | ONSC-SOT-363-6-419B-02_W_V | CMP-013-00037-1 | 1
DMP2035U-7 | Small Signal Field-Effect Transistor, 3.6A I(D), 20V, 1-Element, P-Channel, Silicon, Metal-oxide Semiconductor FET | Q11 | FP-SOT23-IPC_C | CMP-013-00036-1 | 1
RC0603FR-070RL | Fixed Resistor, Metal Glaze/thick Film, 0.1W, 0ohm, Surface Mount, 0603 | R1, R2 | FP-RC0603-MFG | CMP-009-00189-1 | 2
AC0603FR-071ML | Fixed Resistor, Metal Glaze/thick Film, 0.1W, 1000000ohm, 75V, 1% +/-Tol, 100ppm/Cel, Surface Mount, 0603 | R3, R27, R28 | FP-AC0603-IPC_C | CMP-009-00177-1 | 3
RC0603FR-07150RL | Fixed Resistor, Metal Glaze/thick Film, 0.1W, 150ohm, 75V, 1% +/-Tol, 100ppm/Cel, Surface Mount, 0603 | R4, R5, R6 | RESC1608X55X25NL10T15 | CMP-009-00198-1 | 3
RC0603FR-0722K1L | Fixed Resistor, Metal Glaze/thick Film, 0.1W, 22100ohm, 75V, 1% +/-Tol, 100ppm/Cel, Surface Mount, 0603 | R7 | FP-RC0603-0_55-IPC_C | CMP-009-00191-1 | 1
RC0603FR-0710KL | Fixed Resistor, Metal Glaze/thick Film, 0.1W, 10000ohm, 75V, 1% +/-Tol, 100ppm/Cel, Surface Mount, 0603 | R8, R10, R11, R12, R16, R17, R18, R19, R20, R21, R25 | FP-RC0603-0_55-IPC_C | CMP-009-00186-1 | 11
RT0603BRD0747K5L | Fixed Resistor, Thin Film, 0.1W, 47500ohm, 75V, 0.1% +/-Tol, 25ppm/Cel, Surface Mount, 0603 | R9 | FP-RT0603-IPC_C | CMP-009-00192-1 | 1
RC0603FR-072KL | Fixed Resistor, Metal Glaze/thick Film, 0.1W, 2000ohm, 75V, 1% +/-Tol, 100ppm/Cel, Surface Mount, 0603 | R13, R14, R15, R33, R35, R36 | RESC1608X55X25LL10T15 | CMP-009-00188-1 | 6
RC0603FR-07220KL | Fixed Resistor, Metal Glaze/thick Film, 0.1W, 220000ohm, 75V, 1% +/-Tol, 100ppm/Cel, Surface Mount, 0603 | R26 | RESC1608X55X25LL10T15 | CMP-009-00180-1 | 1
AC0603FR-0744K2L | Fixed Resistor, Metal Glaze/thick Film, 0.1W, 44200ohm, 75V, 1% +/-Tol, 100ppm/Cel, Surface Mount, 0603 | R29 | FP-AC0603-IPC_C | CMP-009-00178-2 | 1
RC0603FR-0754K9L | Fixed Resistor, Metal Glaze/thick Film, 0.1W, 54900ohm, 75V, 1% +/-Tol, 100ppm/Cel, Surface Mount, 0603 | R30 | RESC1608X55X25ML10T15 | CMP-009-00179-1 | 1
150080GS75000 | Single Color LED, Green, Water Clear, 1.4mm | STARBOARD | WL-SMCW_0805_150080xx75000 | CMP-007-00045-1 | 1
HSMW-C170-U0000 | BROADCOM LIMITED - HSMW-C170-U0000 - LED | STERN | LEDC2012X90N | CMP-007-00047-1 | 1
KMR221GLFS | Keypad Switch, 1 Switches, SPST, Momentary-tactile, 0.05A, 32VDC, 2.5N, Solder Terminal, Surface Mount-straight | SW1, SW2 | FP-KMR221GLFS-MFG | CMP-011-00013-1 | 2
CP2102N-A02-GQFN28 | USB Bus Controller, CMOS | U1 | FP-CP2102N-A02-GQFN28-IPC_A | CMP-015-00011-2 | 1
L7805CDT-TR | Fixed Positive Standard Regulator, 5VBIPolar, PSSO2 | U3 | TO-252_L | CMP-019-00053-1 | 1
LTC4365ITS8-1#TRPBF | Power Supply Support Circuit, Adjustable, 1 Channel, CMOS, PDSO8 | U4 | FP-TS8-8-05-08-1637-IPC_C | CMP-019-00050-1 | 1
MPU-6050 | Analog Circuit, 1 Func, CMOS | U6 | IS-QFN-24_V | CMP-010-00024-1 | 1
1050170001 | Telecom and Datacom Connector, 5 Contact(s), Female, Right Angle, Surface Mount Terminal, Detent, Receptacle | USB | USB-MICRO-B_V | CMP-002-00073-1 | 1
USBLC6-2SC6 | Trans Voltage Suppressor Diode, 5V V(RWM), Unidirectional, 1 Element, Silicon | USB_ESD | STM-SOT23-6L_V | CMP-015-00009-1 | 1

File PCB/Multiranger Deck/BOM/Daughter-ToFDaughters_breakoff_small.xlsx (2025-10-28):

Comment | Description | Designator | Footprint | LibRef | Quantity
Capacitor 100 nF +/-10% 50 V 0603 | Chip Capacitor, 100 nF, +/- 10%, 50 V, 0603 (1608 Metric) | C6, C7 | CAPC1608X90X40NL10T20 | CMP-001-00017-6 | 2
VL53L1CXV0FY_1 | Integrated Circuit | IC5, IC6 | VL53L1CXV0FY1 | VL53L1CXV0FY_1 | 2
240-004 | Connector | J6, J8 | HDRV6W64P0X254_1X6_1524X254X909P | 240-004 | 2
Resistor 10k +/-1% 0603 100 mW | Chip Resistor, 10 KOhm, +/- 1%, 01 W, -55 to 155 degC, 0603 (1608 Metric) | R4, R5 | RESC1608X55X25ML10T15 | CMP-009-00017-5 | 2

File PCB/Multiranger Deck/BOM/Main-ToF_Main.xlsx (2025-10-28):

Comment | Description | Designator | Footprint | LibRef | Quantity
Capacitor 100 nF +/-10% 50 V 0603 | Chip Capacitor, 100 nF, +/- 10%, 50 V, 0603 (1608 Metric) | C2, C4 | CAPC1608X90X40NL10T20 | CMP-001-00017-6 | 2
Capacitor 4.7µF +/-20% 10V 0603 | Chip Capacitor, 4.7µF +/-20%, 10V, 0603, Thickness 1 mm | C5 | CAPC0603(1608)100_L | CMP-001-00076-4 | 1
PCA9534DWR | Integrated Circuit | IC2 | SOIC127P1030X265-16N | PCA9534DWR | 1
VL53L1CXV0FY_1 | Integrated Circuit | IC3 | VL53L1CXV0FY1 | VL53L1CXV0FY_1 | 1
240-004 | Connector | J1, J3, J5, J7 | HDRV6W64P0X254_1X6_1524X254X909P | 240-004 | 4
Resistor 10k +/-1% 0603 100 mW | Chip Resistor, 10 KOhm, +/- 1%, 01 W, -55 to 155 degC, 0603 (1608 Metric) | R2 | RESC1608X55X25ML10T15 | CMP-009-00017-5 | 1
S4B-XH-A(LF)(SN) | Male Header, Pitch 2.5 mm, 1 x 4 Position, Height 6.1 mm, Tail Length 3.4 mm, -25 to 85 degC, RoHS, Bulk | RANGER_DECK1 | JST-S4B-XH-A(LF)(SN)_V | CMP-002-00034-2 | 1

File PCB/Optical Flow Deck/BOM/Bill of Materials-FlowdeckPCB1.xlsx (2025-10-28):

Comment | Description | Designator | Footprint | LibRef | Quantity
Capacitor 10µF +/-20% 10V 0603 | Chip Capacitor, 10µF +/-20%, 10V, 0603, Thickness 1 mm | C1, C4, C10, C11 | CAPC0603(1608)100_L | CMP-001-00075-4 | 4
Capacitor 100 nF +/-10% 50 V 0603 | Chip Capacitor, 100 nF, +/- 10%, 50 V, 0603 (1608 Metric) | C2, C3, C5, C7, C9 | CAPC1608X90X40NL10T20 | CMP-001-00017-6 | 5
Capacitor 4.7µF +/-20% 10V 0603 | Chip Capacitor, 4.7µF +/-20%, 10V, 0603, Thickness 1 mm | C6, C8 | CAPC0603(1608)100_L | CMP-001-00076-4 | 2
S8B-XH-A(LF)(SN) | Conn Shrouded Header (4 Sides) HDR 8 POS 2.5mm Solder RA Thru-Hole Box | MAIN1 | FP-S8B-XH-A_LF_SN-MFG | CMP-002-00074-1 | 1
PMW3901MB-TXQT | No Description Available | OPTICAL_FLOW1 | QFN_01MB-TXQT_PIX | PMW3901MB-TXQT | 1
Resistor 10k +/-1% 0603 100 mW | Chip Resistor, 10 KOhm, +/- 1%, 01 W, -55 to 155 degC, 0603 (1608 Metric) | R1, R2, R3, R4, R5 | RESC1608X55X25ML10T15 | CMP-009-00017-5 | 5
VL53L1CXV0FY_1 | Integrated Circuit | ToF_SENSOR1 | VL53L1CXV0FY1 | VL53L1CXV0FY_1 | 1
ME6211C18M5G-N | VIN=6.5V Vo=1.8V Io=600mA | U1 | SOT95P245X145-5N | CMP-019-00051-1 | 1

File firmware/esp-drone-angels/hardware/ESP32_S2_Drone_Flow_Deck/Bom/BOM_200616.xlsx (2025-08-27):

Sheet: BOM
BOM V0.1
Item | Quantity | Reference | Value | Package | ICs | Description | Manufacturer | Manufacturer Part # | Notes
1 | 4 | 1C1,1C3,1C7,1C8 | 10uF/10V | C0603 | 陶瓷电容 | 陶瓷电容 | 未指定 | 未指定
2 | 9 | 1C2,1C4,1C6,2C1,2C2,2C3,2C6,1C10,1C11 | 0.1uF/10V | C0402 | 陶瓷电容 | 陶瓷电容 | 未指定 | 未指定
3 | 2 | 1C5,1C9 | 4.7uF/10V | C0603 | 陶瓷电容 | 陶瓷电容 | 未指定 | 未指定
4 | 1 | 2C5 | 4.7uF/10V | C0402 | 陶瓷电容 | 陶瓷电容 | 未指定 | 未指定
5 | 4 | 1J1,1J2,2J1,2J2 | CON8-S-2P0 | CON8-S-2P0 | 连接器 | 单排排母,8P,间距2.0mm,错位贴片,A型 | 长江连接器 | A2005HWV-S-8P-A
6 | 5 | 1R1,1R2,1R3,1R4,1R5 | 10K/1% | R0402 | 贴片电阻 | 贴片电阻 | 未指定 | 未指定
7 | 1 | 1U1 | PMW3901MB-TXQT | COB28_0P65_6X6 | 传感器IC | 光流传感器 | PixArt Imaging | PMW3901MB-TXQT | 需同时采购配套镜头
8 | 1 | 1U2 | ME6211C20M5G-N | SOT-23-5 | LDO IC | LDO,输出电压2.0V | 微盟电子 | ME6211C20M5G-N
9 | 1 | 1U3 | VL53L1CXV0FY/1 | LGA12_0P8_2P5X4P9 | 传感器IC | ToF传感器 | ST | VL53L1CXV0FY/1
10 | 1 | 2C4 | 0.22uF/10V | C0402 | 陶瓷电容 | 陶瓷电容 | 未指定 | 未指定
11 | 1 | 2U1 | HMC5833L | LPCC16_0P5_3X3 | 传感器IC | Compass传感器 | Honeywell | HMC5833L
12 | 1 | 2U2 | MS5611-01BA | QFN8_1P25_3X5 | 传感器IC | 气压传感器 | TE | MS5611-01BA

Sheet: Changelog
版本 | 改版内容 | 改版人 | 改版日期
V0.1 | 首版 | YXF | 2020-06-12

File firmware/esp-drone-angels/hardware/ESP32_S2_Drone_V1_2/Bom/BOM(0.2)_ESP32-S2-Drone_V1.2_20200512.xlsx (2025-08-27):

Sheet: ESP32-S2-Drone
BOM(V0.2)_ESP32-S2-Drone_V1.2
ID | Qty | Ref Des | Value | Package | Description | Manufacturer | Manufacturer Part # | Notes
1 | 8 | C1,C3,C10,C11,C12,C14,C15,C16 | 10uF/10V | C0603 | 陶瓷电容
2 | 9 | C2,C4,C5,C7,C9,C17,C18,C19,C21 | 0.1uF/10V | C0402 | 陶瓷电容
3 | 2 | C6,C8 | 4.7uF/10V | C0603 | 陶瓷电容
4 | 1 | C13 | 470pF/25V | C0402 | 陶瓷电容
5 | 1 | C20 | 10nF/25V | C0402 | 陶瓷电容
6 | 1 | C22 | 2.2nF/25V | C0402 | 陶瓷电容
7 | 0 | C23,C24 | 0.1uF/10V(NC) | C0402 | 陶瓷电容 |  |  | 不贴件
8 | 4 | D1,D2,D4,D5 | 1N4148WT | SOD523 | 开关二极管 | 长电科技 | 1N4148WT
9 | 1 | D3 | BAT60B | SOD323 | 肖特基二极管 | Infineon | BAT60B
10 | 1 | D6 | LED-WHT | LED3010-S | LED,白色 | Everlight | 12-21/T3D-APQHY/2C
11 | 1 | D7 | LED-BLE | LED3010-S | LED,蓝色 | Everlight | 12-21/BHC-ZL2N1TY/2C
12 | 1 | D8 | LED-RED | LED3010-S | LED,红色 | Everlight | 12-21/R8C-AN1P2B/2D
13 | 1 | D9 | LED-GRN | LED3010-S | LED,绿色 | Everlight | 12-21/GHC-YQ1R1B18Y/2C
14 | 1 | FB1 | BLM18SG331TN1D | L0603 | 磁珠,330R at 100MHz,1A | Murata | BLM18SG331TN1D
15 | 1 | J1 | USB-MICRO-B | USB_5P_MICRO_F | USB MicroB 连接器,四脚插板,无柱,卷边
16 | 1 | J2 | FFC-24P | FFC24-0P5 | FPC连接器,24P,间距0.5MM,翻盖式,下接
17 | 4 | J3,J4,J10,J11 | CON8-S-2P54 | A2005HWV-S-XP-A | 单排排母,8P,间距2.0mm,错位贴片,A型 | 长江连接器 | A2005HWV-S-8P-A
18 | 0 | J5,J6,J8,J9 | CON2-SB-ZH(NC) | CON2X1_1P5_SMT_ZH-2A_DIP | 针座,2P,ZH,侧入贴片 |  |  | 不贴件
19 | 1 | J7 | CON2-SB-PH | CON2X1_2P0_SMT_PH2A-S-A | 针座,2P,PH,侧入贴片
20 | 1 | Q3 | AO3401A | SOT-23-3 | PMOS | AOS | AO3401A
21 | 4 | Q4,Q5,Q6,Q7 | IRLML6344TRPbF | SOT-23-3 | Power NMOS | Infineon | IRLML6344TRPbF
22 | 3 | R1,R3,R6 | 0R/1% | R0402 | 贴片电阻
23 | 19 | R5,R8,R11,R12,R13,R14,R15,R16,R21,R22,R23,R24,R25,R27,R28,R32,R33,R34,R35 | 10K/1% | R0402 | 贴片电阻
24 | 1 | R7 | 22.1K/1% | R0402 | 贴片电阻
25 | 1 | R9 | 47.5K/1% | R0402 | 贴片电阻
26 | 3 | R10,R17,R19 | 82K/1% | R0402 | 贴片电阻
27 | 1 | R18 | 52.3K/1% | R0402 | 贴片电阻
28 | 1 | R20 | 29.4K/1% | R0402 | 贴片电阻
29 | 4 | R26,R29,R30,R31 | 1.5K/1% | R0402 | 贴片电阻
30 | 2 | SW1,SW2 | Button-3X3.5 | SW4_3X3P5X1P1_SMT | 轻触开关,侧按贴片,3mmX3.5mm | ALPS | SKSCLBE010
31 | 1 | U1 | USBLC6-2SC6 | SOT23-6 | ESD二极管 | ST | USBLC6-2SC6
32 | 1 | U2 | ME6211C28M5G-N | SOT-23-5 | LDO,2.8V | 微盟 | ME6211C28M5G-N
33 | 1 | U3 | CP2102N-A02 | QFN28_0P5_5 | USB to UART IC | Silicon Labs | CP2102N-A02
34 | 1 | U4 | ME6211C15M5G-N | SOT-23-5 | LDO,1.5V | 微盟 | ME6211C15M5G-N
35 | 1 | U5 | SGM2205-ADJ | DFN3030-8 | LDO,可调 | 圣邦微 | SGM2205-ADJ
36 | 1 | U6 | ESP32-S2-WROVER | ESP32-S2-WROVER | WiFi Module | Espressif | ESP32-S2-WROVER
37 | 1 | U7 | MPU-6050 | QFN24_0p5_4_A | 6轴运动传感器IC | InvenSense | MPU-6050
38 | 1 | U8 | BC847BDW1T1G | SOT363 | NPN Transistor,双路 | ON Semi | BC847BDW1T1G
39 | 1 | 非贴片物料 | 无人机锂电池 | NA | 动力型,300mAh,PH2.0,正向 |  |  | 参考链接 https://m.tb.cn/h.V8gEksR?sm=858897
40 | 4 | 非贴片物料 | 空心杯电机 | NA | 尺寸716,电压3.7v,50000转 |  |  | 参考链接 https://m.tb.cn/h.VR4sgSA?sm=2d0222
41 | 2 | 非贴片物料 | 螺旋桨A | NA | 尺寸46mm,0.75mm孔径,A螺旋桨 |  |  | 参考链接 https://m.tb.cn/h.VinQLQu?sm=185f2b
42 | 2 | 非贴片物料 | 螺旋桨B | NA | 尺寸46mm,0.75mm孔径,B螺旋桨 |  |  | 参考链接 https://m.tb.cn/h.VinQLQu?sm=185f2b
43 | 4 | 非贴片物料 | 电机密封圈 | NA | 孔径7mm,黑色 |  |  | 参考链接 https://m.tb.cn/h.VRfYUIN?sm=1dbc9d

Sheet: Sheet2
39 | 1 | NA | 无人机锂电池 | NA | 动力型300mah PH2.0 正向 | 参考链接 https://m.tb.cn/h.V8gEksR?sm=858897
40 | 4 | NA | 空心杯电机 | NA | 尺寸716 电压3.7v 50000 | 参考链接 https://m.tb.cn/h.VR4sgSA?sm=2d0222
41 | 2 | NA | 螺旋桨A | NA | 尺寸46mm 0.75mm孔径 A螺旋桨 | 参考链接 https://m.tb.cn/h.VinQLQu?sm=185f2b
42 | 2 | NA | 螺旋桨B | NA | 尺寸46mm 0.75mm孔径 B螺旋桨 | 参考链接 https://m.tb.cn/h.VinQLQu?sm=185f2b
43 | 4 | NA | 电机密封圈 | NA | 7mm孔径黑色 | 参考链接 https://m.tb.cn/h.VRfYUIN?sm=1dbc9d

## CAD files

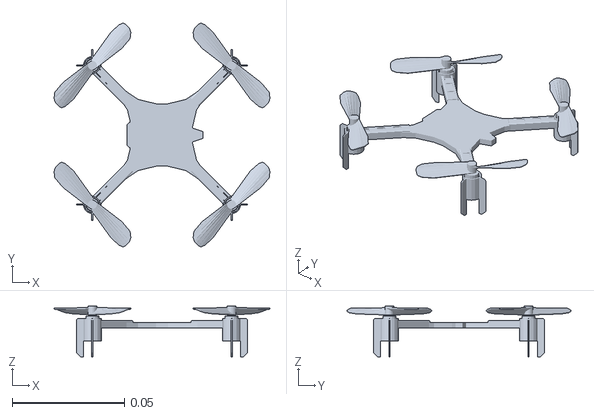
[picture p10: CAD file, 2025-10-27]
Software/GSC/MRD workspace/crazyflie_mapping_demo/ros2_ws/src/crazyswarm2/crazyflie/urdf/cf2_assembly.stl
0.0963 x 0.0998 x 0.0225

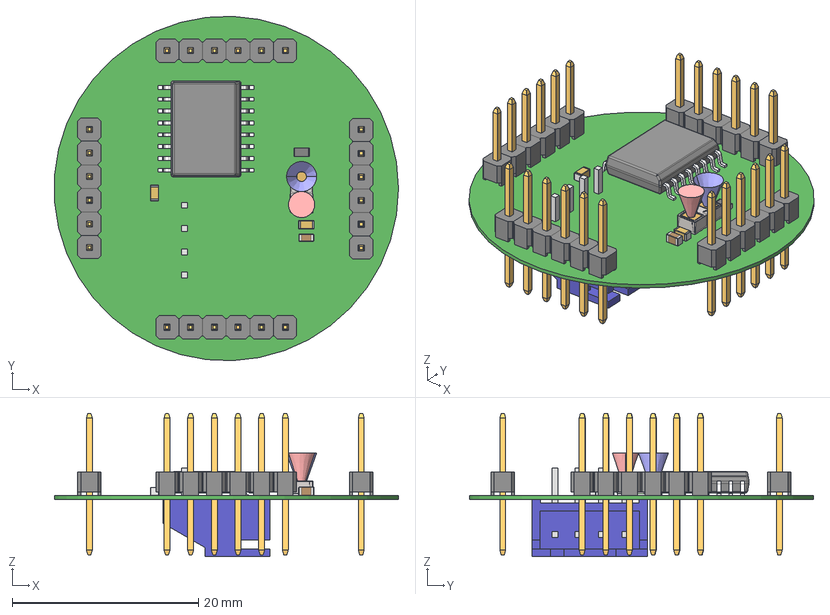
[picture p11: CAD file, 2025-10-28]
PCB/Multiranger Deck/ExportSTEP/ToF_Main.step
36.9 x 37.0 x 15.4 mm
S4B-XH-A
Mid_Body
Mark
VL53L1 Module outline
VL53L1 Exclusion cones
BODY-SOIC
LEAD-DW0016 x 16
CAPC1608X95N EIA 0603

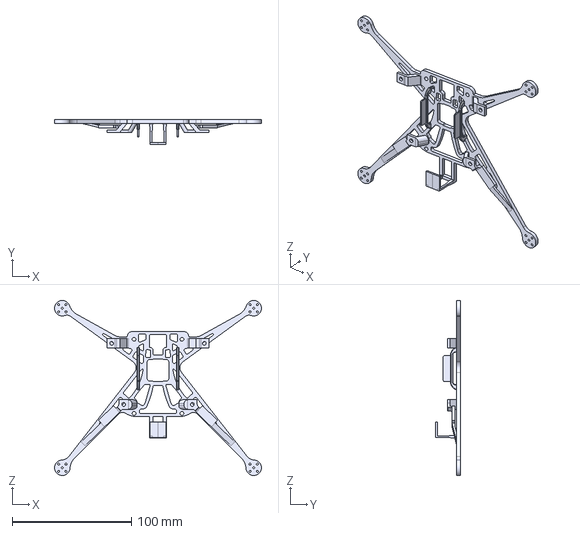
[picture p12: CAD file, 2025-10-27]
frame/STEP files/Main_Frame_V9_escm.step
173.2 x 20.5 x 146.5 mm

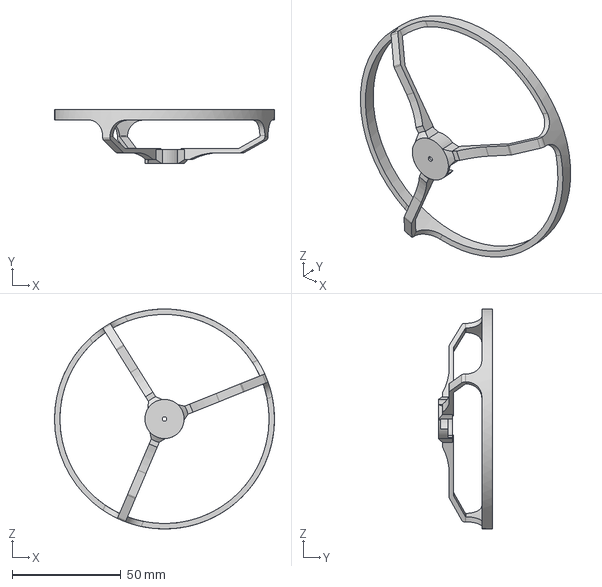
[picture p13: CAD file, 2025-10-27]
frame/STEP files/Frnt_Guard_V6_filround.step
101.0 x 25.0 x 101.0 mm

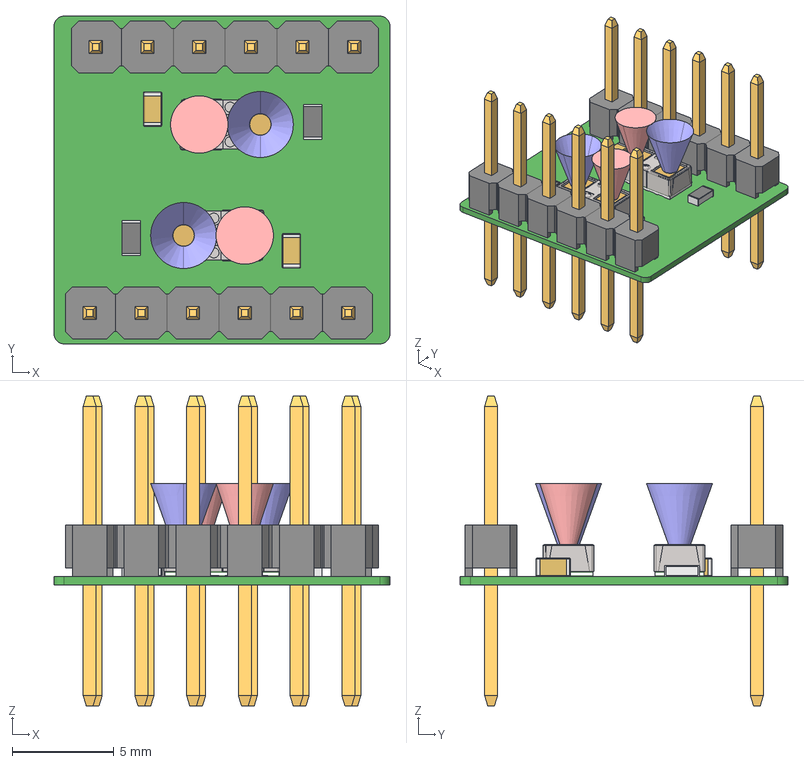
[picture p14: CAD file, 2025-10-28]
PCB/Multiranger Deck/ExportSTEP/ToFDaughters_breakoff_small.step
16.5 x 16.1 x 15.2 mm
Mid_Body x 2
Mark x 2
VL53L1 Module outline x 2
VL53L1 Exclusion cones x 2

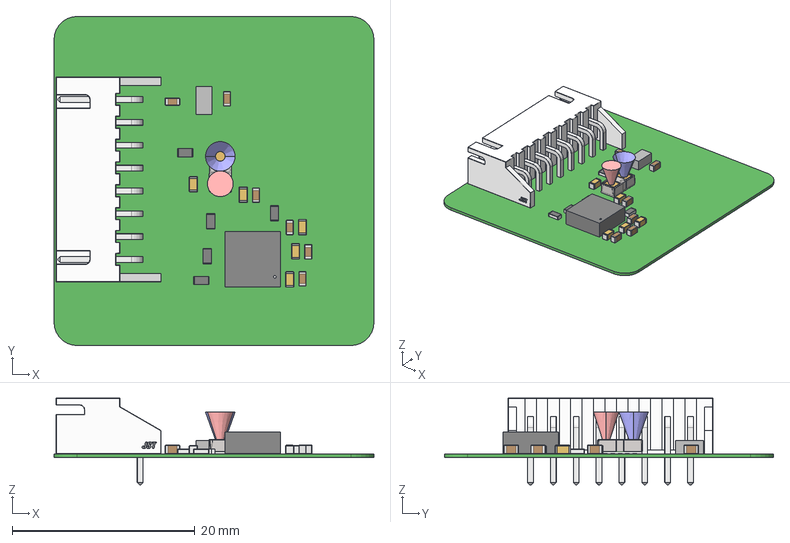
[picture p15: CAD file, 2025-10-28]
PCB/Optical Flow Deck/ExportSTEP/FlowdeckPCB1.step
35.0 x 36.0 x 9.50 mm
Pin1_Triangle
JST
Extruded
VL53L1 Module outline
VL53L1 Exclusion cones
Mid_Body x 5
Mark x 5
CAPC1608X95N EIA 0603 x 6

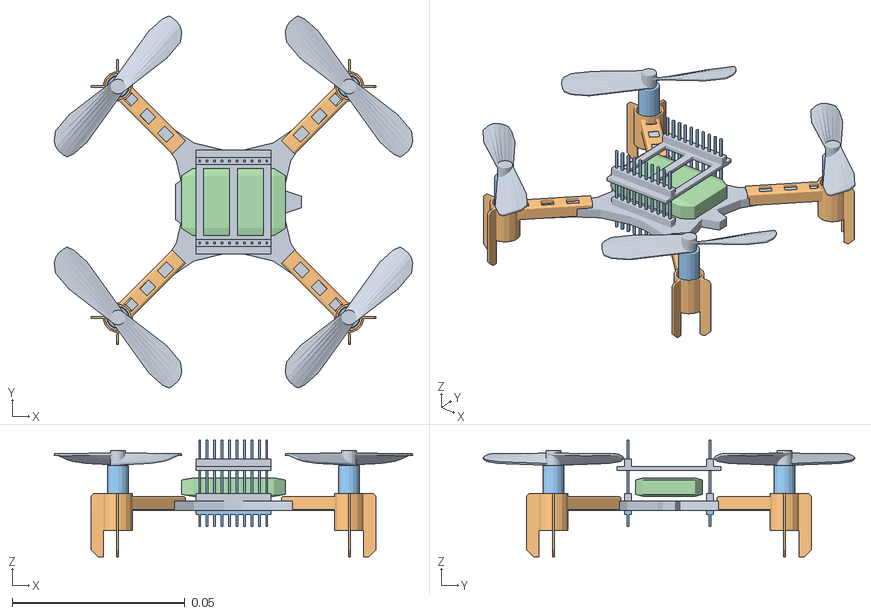
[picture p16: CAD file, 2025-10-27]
Software/GSC/MRD workspace/crazyflie_mapping_demo/ros2_ws/src/crazyswarm2/crazyflie_sim/crazyflie_sim/visualization/data/model/cf.obj
0.104 x 0.108 x 0.0339
cf_pcb
cf_Material.002
cf_metal
cf_Material.001

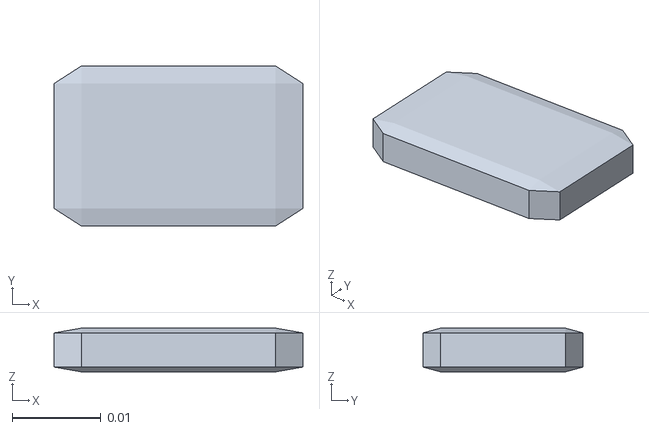
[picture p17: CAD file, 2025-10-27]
Software/GSC/MRD workspace/crazyflie_mapping_demo/simulation_ws/crazyflie-simulation/meshes/stl_files/battery.stl
0.028 x 0.018 x 0.00492

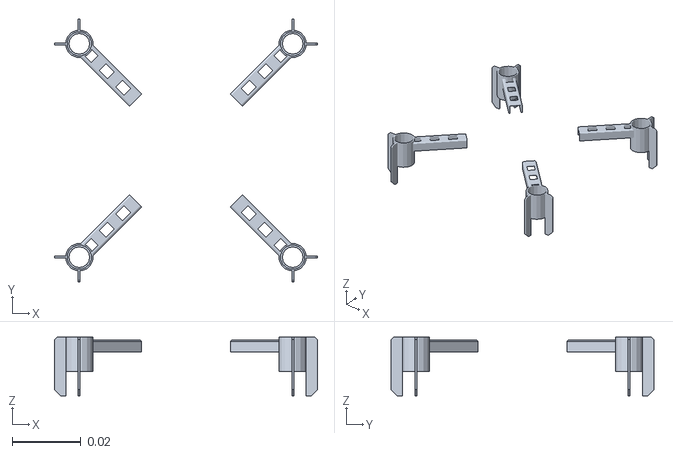
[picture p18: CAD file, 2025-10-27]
Software/GSC/MRD workspace/crazyflie_mapping_demo/simulation_ws/crazyflie-simulation/meshes/stl_files/4_motormounts.stl
0.0764 x 0.0764 x 0.017

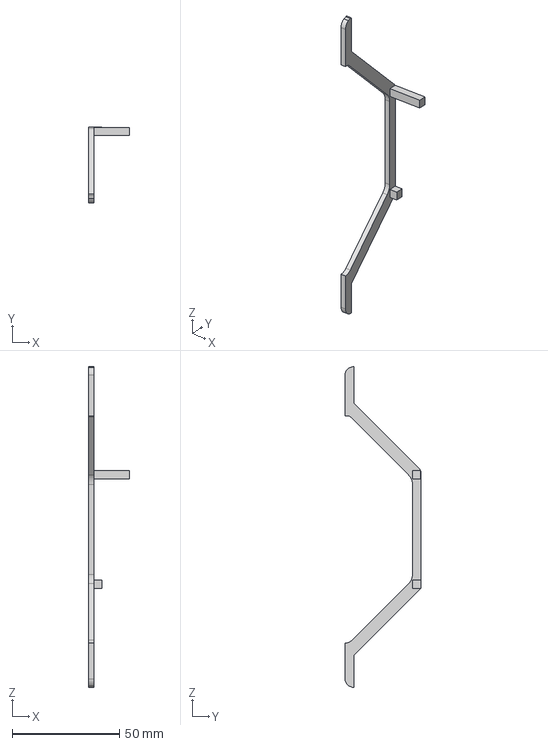
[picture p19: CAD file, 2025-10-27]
frame/STEP files/Big_leg_V2_light.step
19.1 x 35.4 x 149.5 mm

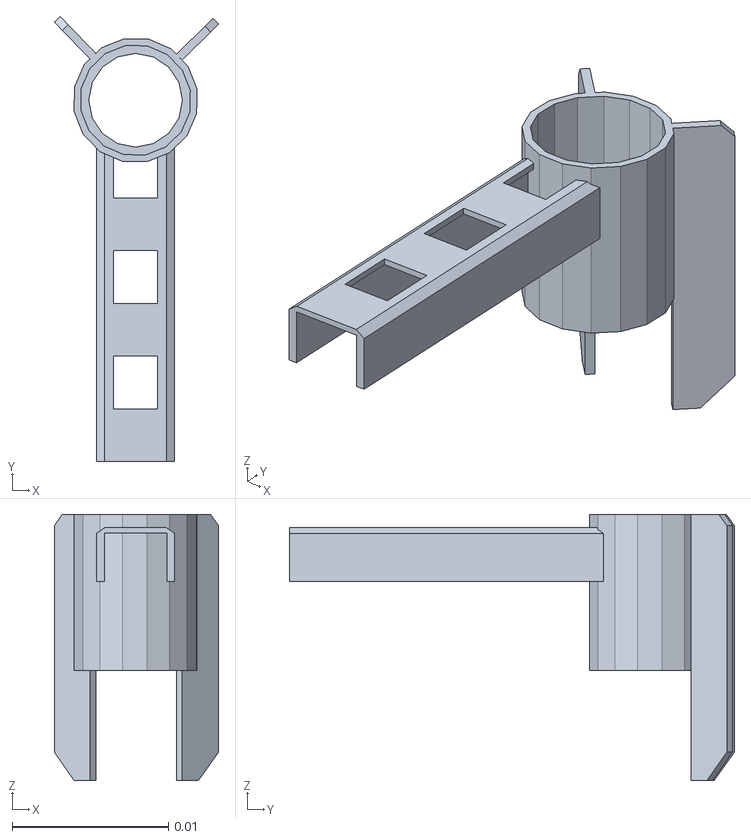
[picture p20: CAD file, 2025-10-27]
Software/GSC/MRD workspace/crazyflie_mapping_demo/simulation_ws/crazyflie-simulation/meshes/stl_files/motor_mount.stl
0.0105 x 0.0285 x 0.017

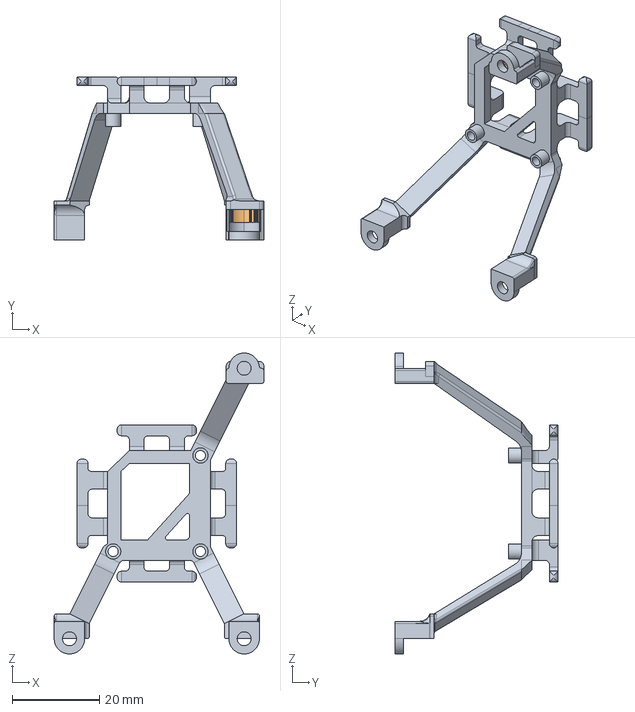
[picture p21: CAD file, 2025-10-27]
frame/STEP files/Top_Deck_V6_protective.step
48.1 x 37.4 x 69.0 mm

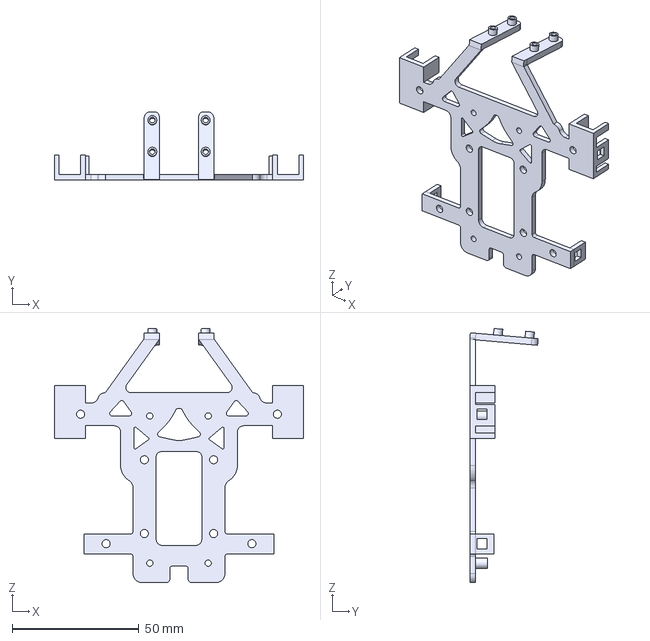
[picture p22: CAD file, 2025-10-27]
frame/STEP files/Bottom_Plate_V5_light.step
98.1 x 27.0 x 100.1 mm

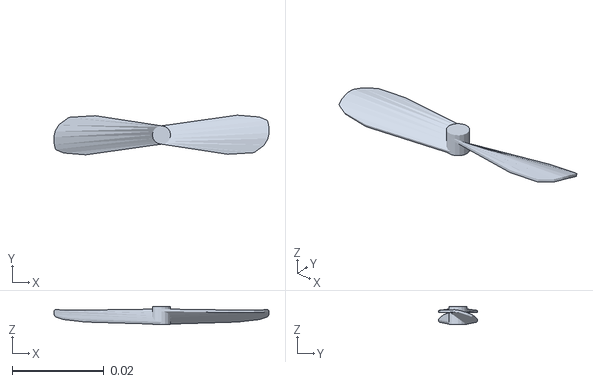
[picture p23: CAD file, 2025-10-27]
Software/GSC/MRD workspace/crazyflie_mapping_demo/simulation_ws/crazyflie-simulation/meshes/stl_files/ccw_prop.stl
0.047 x 0.00867 x 0.004

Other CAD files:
frame/STEP files/Rear_Guard_V6_fixedmaybe.step
Software/GSC/MRD workspace/crazyflie_mapping_demo/simulation_ws/crazyflie-simulation/meshes/stl_files/cw_prop.stl
frame/STEP files/Test_leg_1.step
Software/GSC/MRD workspace/crazyflie_mapping_demo/simulation_ws/crazyflie-simulation/meshes/blender_files/battery.blend
Software/GSC/MRD workspace/crazyflie_mapping_demo/simulation_ws/crazyflie-simulation/meshes/blender_files/battery_holder.blend
Software/GSC/MRD workspace/crazyflie_mapping_demo/simulation_ws/crazyflie-simulation/meshes/blender_files/cf2_assembly.blend
Software/GSC/MRD workspace/crazyflie_mapping_demo/simulation_ws/crazyflie-simulation/meshes/blender_files/cf_body.blend
Software/GSC/MRD workspace/crazyflie_mapping_demo/simulation_ws/crazyflie-simulation/meshes/blender_files/cw_prop.blend
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

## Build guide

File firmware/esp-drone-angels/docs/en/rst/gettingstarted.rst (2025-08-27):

================
Get Started 
================

:link_to_translation:`zh_CN:[中文]`

ESP-Drone Overview
======================

ESP-Drone is an ESP32/ESP32-S2/ESP32-S3 based flying development board provided by Espressif. ESP-Drone is equipped with Wi-Fi key features, which allows this drone to be connected to and controlled by an APP or a gamepad over a Wi-Fi network. This drone comes with simple-structured hardware, clear codes, and supports functional extension. Therefore, ESP-Drone can be used in STEAM education. Part of the codes is from Crazyflie open source project under GPL3.0
license.

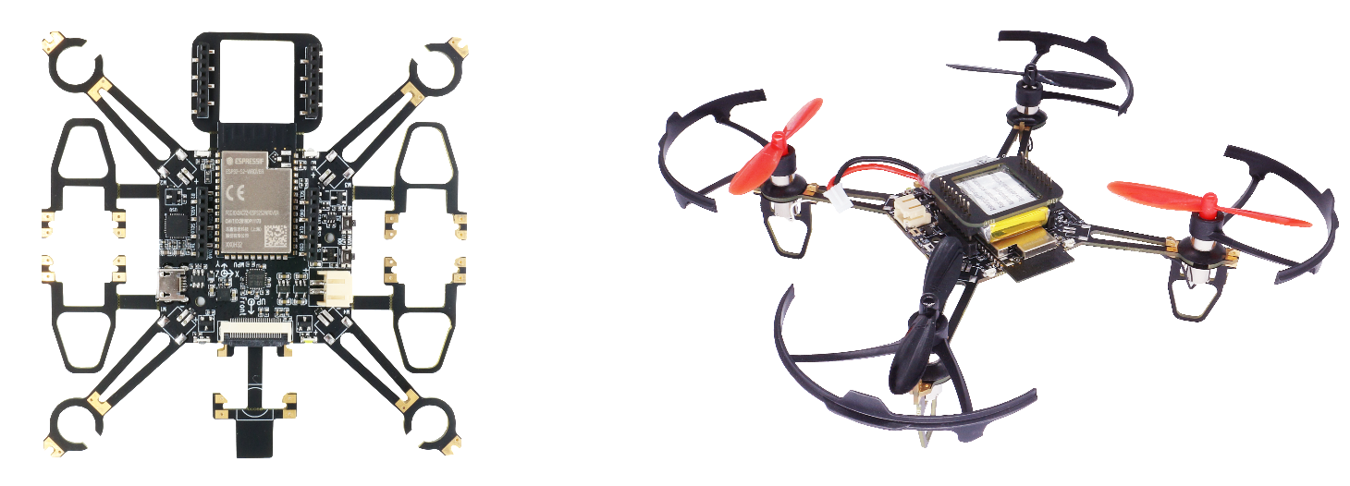
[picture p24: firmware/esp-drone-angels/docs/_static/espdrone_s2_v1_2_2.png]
ESP-Drone

   
   ESP-Drone

Main Features
----------------

ESP-Drone has the following features:

- Stabilize mode: keep the drone stable to achieve smooth flight.
- Height-hold mode: control thrust output to keep the drone flying at a fixed height.
- Position-hold mode: keep the drone flying at a fixed position.
- PC debugging: use cfclient for static/dynamic debugging.
- Controlled by APP: easily controlled over Wi-Fi by your mobile APP.
- Controlled by gamepad: easily controlled via the gamepad by cfclient.

Main Components
----------------

ESP-Drone 2.0 consists of a main board and several extension boards:

-  **Main board**: integrates an ESP32-S2 module, necessary sensors for basic flight, and provides hardware extension interfaces.
-  **Extension boards**: integrate extension sensors via hardware extension interfaces of the main board, to implement advanced flight.  

.. list-table:: 
   :widths: 4 20 15 15 10 10
   :header-rows: 1

   * - No.
     - Modules
     - Main Components
     - Function
     - Interfaces
     - Mount Location
   * - 1
     - Main board - **ESP32-S2**
     - ESP32-S2-WROVER + MPU6050
     - Basic flight
     - I2C, SPI, GPIO, extension interfaces
     - 
   * - 2
     - Extension board - **Position-hold module**
     - PMW3901 + VL53L1X
     - Indoor position-hold flight
     - SPI + I2C
     - Mount at bottom, facing to the ground.
   * - 3
     - Extension board - **Pressure module**
     - MS5611 pressure module
     - Height-hold flight
     - I2C or MPU6050 slave
     - Mount at the top or at the bottom
   * - 4
     - Extension board - **Compass module**
     - HMC5883 compass
     - Advanced flight mode, such as head-free mode
     - I2C or MPU6050 slave
     - Mount at the top or at the bottom

For more information, please refer to `Hardware Reference <./hardware.rst>`__.

ESP-IDF Overview
================

ESP-IDF is the IoT Development Framework provided by Espressif for ESP32/ESP32-S2/ESP32-S3.

- ESP-IDF is a collection of libraries and header files that provides the core software components that are required to build any software projects on ESP32/ESP32-S2.

- ESP-IDF also provides tools and utilities that are required for typical developer and production use cases, like build, flash, debug and measure. 

For more information, please check `ESP-IDF
Programming Guide <https://docs.espressif.com/projects/esp-idf/en/release-v5.0/esp32s2/get-started/index.html>`__.

Crazyflie Overview
=======================

Crazyflie is a Bitcraze open-source quadcopter, with the following features:

- Support various sensor combinations for advanced flight modes, such as Height-hold mode and Position-hold mode.
- Based on FreeRTOS, which allows users to break down complex drone systems into multiple software tasks with various priorities.
- Customized full-featured cfclient and CRTP communication protocol, for debug, measurement, and control purposes.

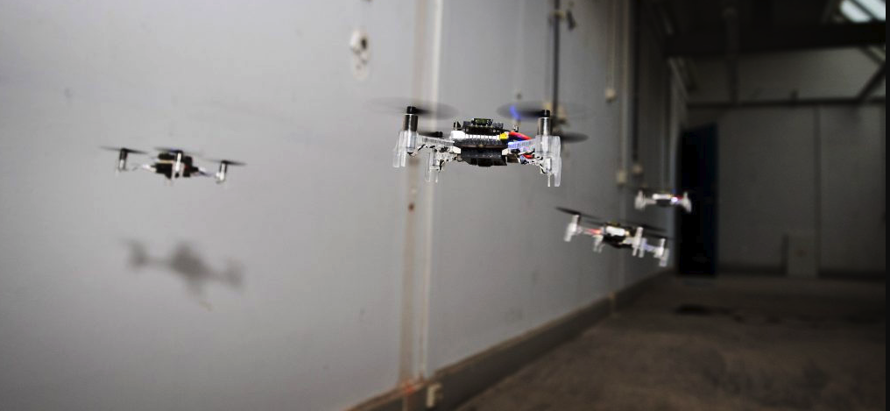
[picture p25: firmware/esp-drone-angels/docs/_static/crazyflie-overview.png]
crazyflie-overview

   
   `A swarm of drones exploring the environment, avoiding obstacles
   and each other. (Guus Schoonewille, TU Delft) <https://img-blog.csdnimg.cn/20191030202634944.jpg?x-oss-process=image/watermark,type_ZmFuZ3poZW5naGVpdGk,shadow_10,text_aHR0cHM6Ly9ibG9nLmNzZG4ubmV0L3FxXzIwNTE1NDYx,size_16,color_FFFFFF,t_70>`__

For more information, see `Crazyflie <https://www.bitcraze.io/>`__.

Preparations
================

Assemble Hardware
--------------------

Please follow the steps below to assemble ESP32-S2-Drone V1.2.

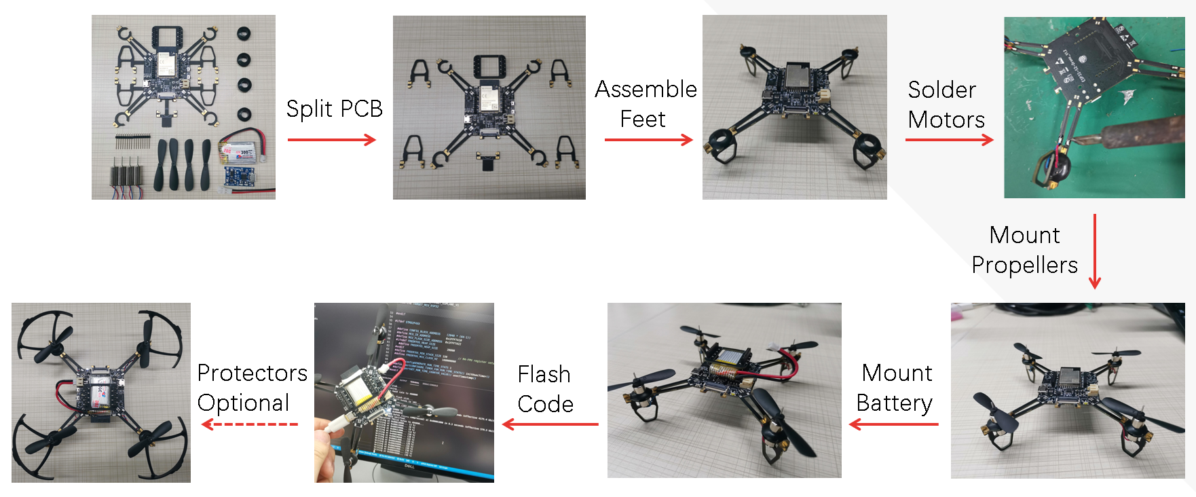
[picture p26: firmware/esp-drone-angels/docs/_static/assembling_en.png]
ESP32-S2-Drone V1.2 Assemble Flow

   
   ESP32-S2-Drone V1.2 Assemble Flow

Hardware overview and pin allocation are available at: `Hardware Reference <./hardware.rst>`__.

Download and Install ESP-Drone APP
----------------------------------------
ESP-Drone APP is available for Android and iOS.

For Android, please scan the QR below to download ESP-Drone APP.

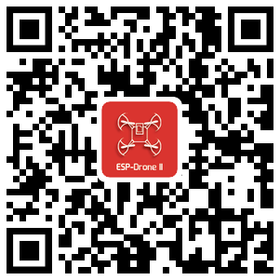
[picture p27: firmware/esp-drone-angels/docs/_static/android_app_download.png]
Android APP QR


For iOS, please search and download the ESP-Drone APP in App Store.

iOS APP source code:
`ESP-Drone-iOS <https://github.com/EspressifApps/ESP-Drone-iOS>`__

Android APP source code:
`ESP-Drone-Android <https://github.com/EspressifApps/ESP-Drone-Android>`__

Install cfclient
--------------------

This step is optional, only for advanced debugging.

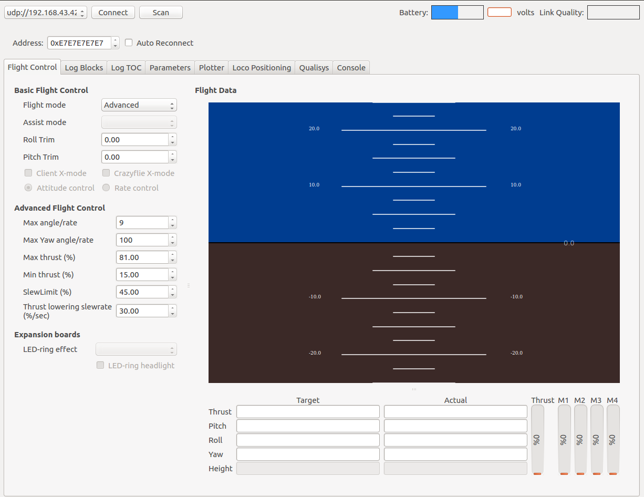
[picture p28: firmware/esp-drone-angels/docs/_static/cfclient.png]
cfclient Interface


   cfclient Interface

**1. Install cfclient**

1.1 Download the source code

.. code:: text

   git clone https://github.com/qljz1993/crazyflie-clients-python.git

1.2 Check into the directory

.. code:: text

   cd crazyflie-clients-python

1.3 Install cfclient

.. code:: text

   pip3 install -e .

1.4 Start cfclient

.. code:: text

   cfclient

**2. Configure the controllers**

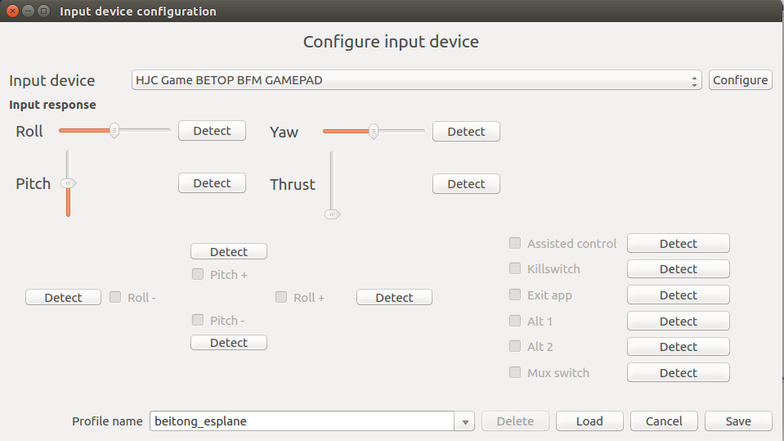
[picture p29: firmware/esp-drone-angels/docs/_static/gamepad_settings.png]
Controller Configuration


   Controller Configuration

2.1 Configure the four main dimensions of controls: ``Roll, Pitch, Yaw, Thrust``.

2.2 Configure button ``Assisted control`` for flight mode switching.

ESP-Drone APP Guide
=====================

Establish Wi-Fi connection
---------------------------
* Scan Wi-Fi AP on your mobile. ESP-Drone device works as a Wi-Fi AP with the following SSID:  

::

   SSID: ESP-DRONE_XXXX (XXXX is configured based on MAC) PASSWORD: 12345678

* Click this AP, connect your mobile to this AP.

Now a Wi-Fi connection is established between your mobile and your drone.

Customize settings
---------------------------
In this step, you can customize the flight settings according to your application scenarios, or use the default configuration below.

::

   ```
   Default configuration:

   Flight control settings 
       1. Mode: Mode2
       2. Deadzone: 0.2
       3. Roll trim: 0.0
       4. Pitch trim: 0.0
       5. Advanced flight control: true
       6. Advanced flight control preferences 
           1. max roll/pitch angle: 15
           2. max yaw angle: 90
           3. max thrust: 90
           4. min thrust: 25
           5. X-Mode: true
   Controller settings 
       7. use full travel for thrust: false
       8. virtual joystick size: 100
   App settings
       9. Screen rotation lock: true
       10. full screen mode:true
       11. show console: true   
   ```

Flight Control
---------------------

- Click “Connect” button/icon at your APP. When the connection is established successfully between your drone and APP, the LED on the drone blinks GREEN.
- Slide “Thrust” slightly to take off the drone.
- Control the flight by moving your fingers on the APP.

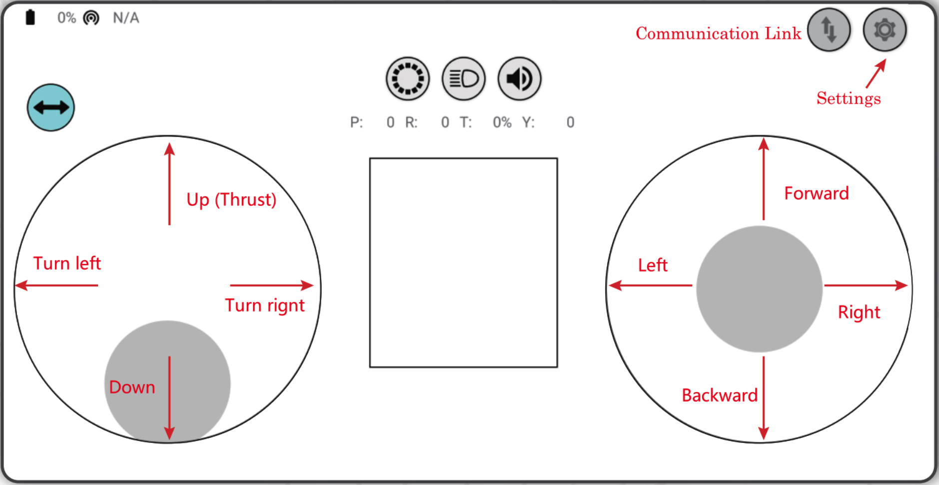
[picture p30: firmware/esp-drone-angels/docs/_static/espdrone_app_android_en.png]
Android APP Interface


   Android APP Interface

PC cfclient Guide
======================

Cfclient is the PC client for ``Crazeflie`` source project, which has fully implemented the functions defined in ``CRTP`` and makes the drone debugging faster. ESP-Drone customizes this cfclient to meet functional design needs.

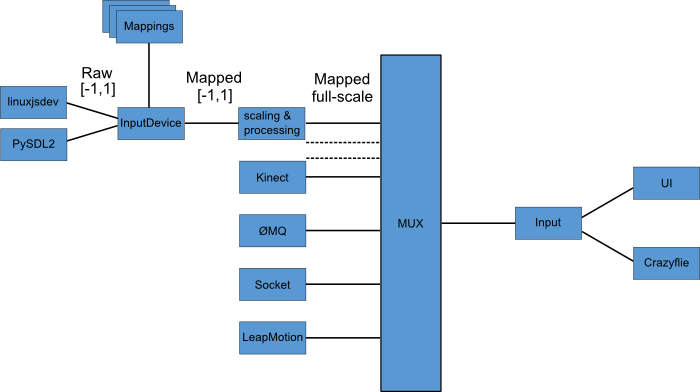
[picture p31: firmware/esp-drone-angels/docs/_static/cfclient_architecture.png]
cfclient architecture


   Cfclient Architecture

cfclient console interface

   Cfclient Console Interface

In this project, we have configuration files and cache files. JSON file is used to store configuration information. For more information about the configuration, please refer to `User
Configuration File <https://www.bitcraze.io/documentation/repository/crazyflie-clients-python/master/development/dev_info_client/>`__.

Flight Settings
--------------------

Basic Flight Control
~~~~~~~~~~~~~~~~~~~~~~

1. Flight mode: normal and advanced modes

   - Normal mode: for beginners.
   - Advanced mode: unlock the maximum angle and the maximum thrust.

2. Assisted mode

   - Altitude-hold mode: maintain flight altitude. To implement this mode, a barometric pressure sensor is needed.
   - Position-hold mode: maintain current flight position. To implement this mode, an optical flow sensor and a Time of Flight (TOF) sensor are needed.
   - Height-hold mode: keep flight height. Note: to apply this mode, the drone should fly at 40 cm or higher over the ground, and a TOF is needed.
   - Hover mode: stay and hover at 40 cm or higher over the take-off point. To implement this mode, a optical flow sensor and a TOF are needed.

3. Trim

   - Roll Trim: trim the rotation around a horizontal axis going through the drone from back to front. This rotation literally rolls the drone and moves it left and right. Roll trim is used to compensate for the level installation deviation of sensors.
   - Pitch Trim: trim the rotation around a horizontal axis going through the drone from left to right. This rotation tilts the drone and moves it forwards or backwards. Pitch trim is used to compensate for the level installation deviation of sensors.

Note that in assisted mode, the thrust controller works as a height controller.

Advanced Flight Control
~~~~~~~~~~~~~~~~~~~~~~~~

1. Max angle: set the maximum pitch and roll rotation: roll/pitch.
2. Max yaw rate: set the allowed yaw: ``yaw``.
3. Max thrust: set the maximum thrust.
4. Min thrust: set the minimum thrust.
5. Slew limit: prevent sudden drop of thrust. When the thrust drops below this limit, the rates below ``Slew rate`` will not be allowed.
6. Slew rate: this is the maximum rate when the thrust is below ``slew limit``.

Configure Input Device
~~~~~~~~~~~~~~~~~~~~~~~~~~~~~

Follow the prompts, route the controllers to each channel.

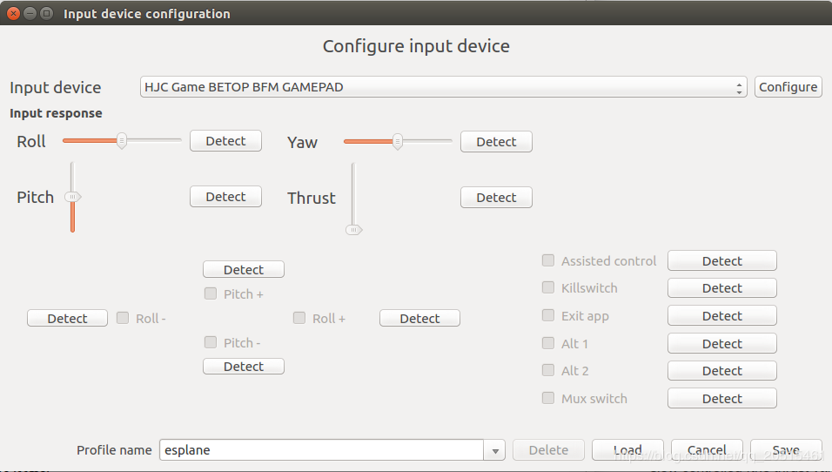
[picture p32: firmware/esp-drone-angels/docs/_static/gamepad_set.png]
cfclient input device configuration


   Cfclient Input Device Configuration

Flight Data
~~~~~~~~~~~~~~~~

On the tab “Flight Control” of cfclient, you can check the drone status. The detailed information is shown at the bottom right, including:

1. Target: target angle
2. Actual: measured angle
3. Thrust: current thrust value
4. M1/M2/M3/M4: actual output of motors

Tune Online Parameters
--------------------------

**Tune PID parameters online**

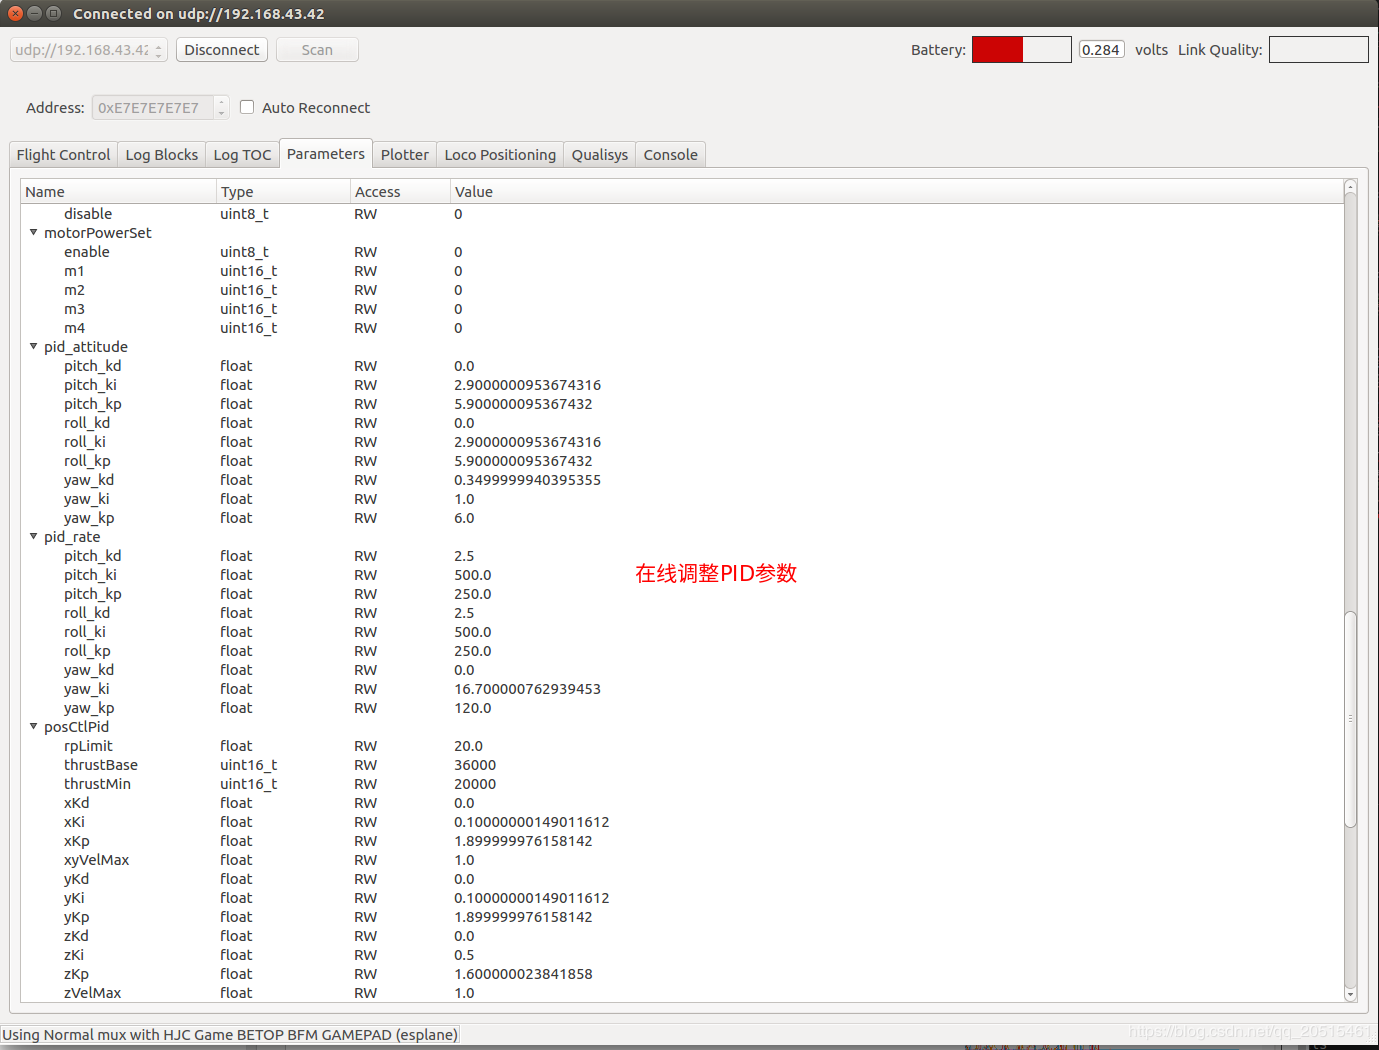
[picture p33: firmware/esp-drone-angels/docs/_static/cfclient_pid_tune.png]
PID parameters tunning

   
   Cfclient PID Parameters Tunning

**Note**

1. The modified parameters take effect in real time, which avoids frequent flash of firmware.
2. You can define in your code which parameters can be modified by PC in real time.
3. Note that modifying parameters online is only for debugging purpose. The modified parameters will not be saved at power down.

Monitor Flight Data
-----------------------

Configure the parameters to monitor at Tab Log configuration and Tab Log Blocks:

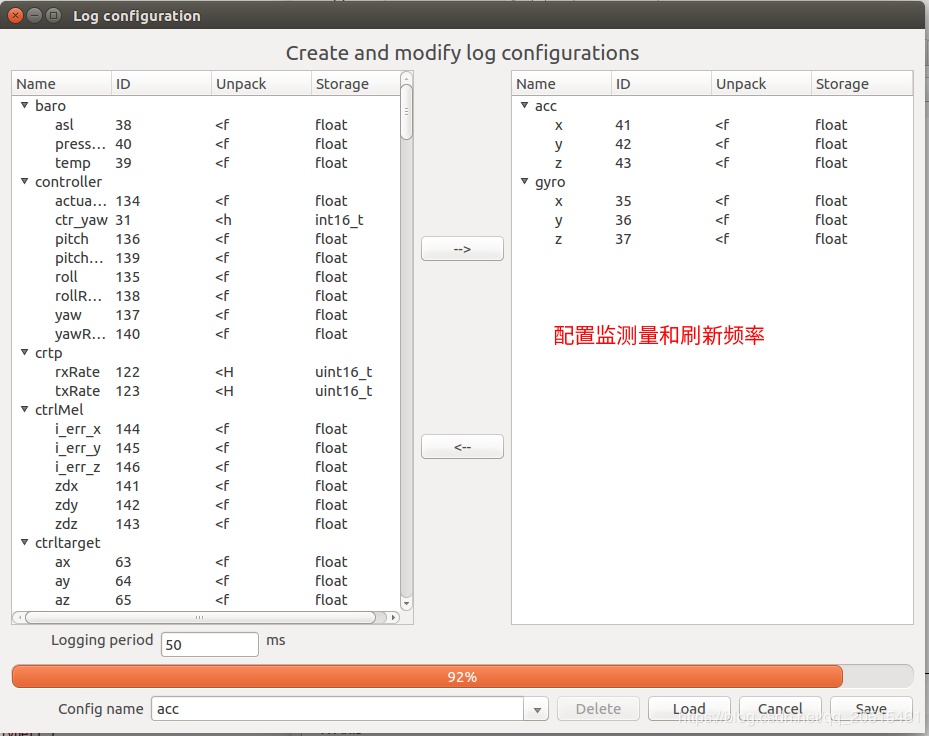
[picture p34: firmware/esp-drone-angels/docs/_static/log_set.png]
Log configuration

   
   Log Configuration

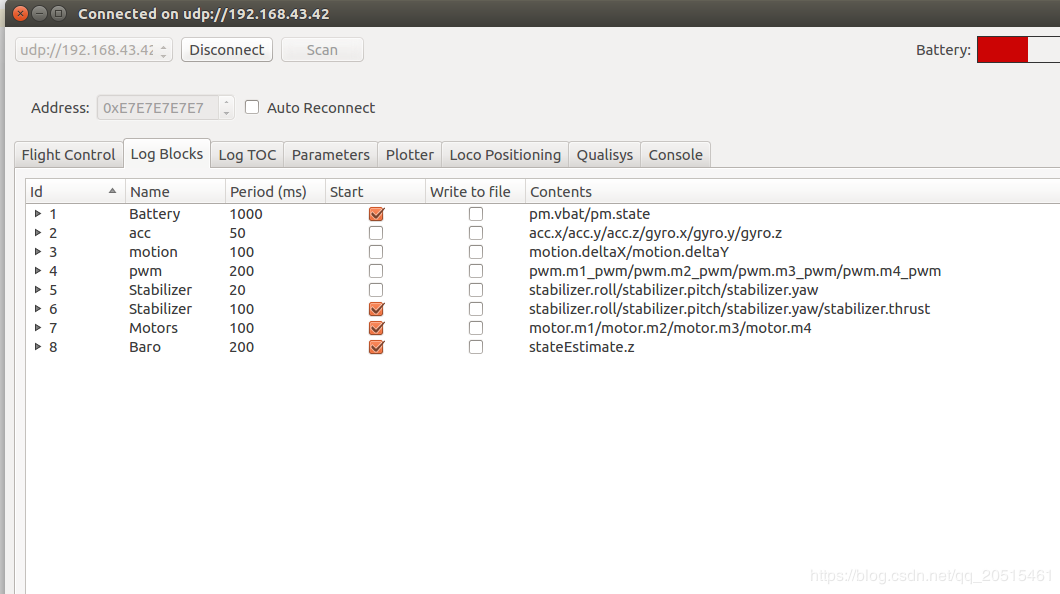
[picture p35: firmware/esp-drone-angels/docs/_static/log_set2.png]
Log Blocks

   
   Log Blocks

Configure real-time waveform drawing at Tab Plotter, to monitor gyro accelerometer data.

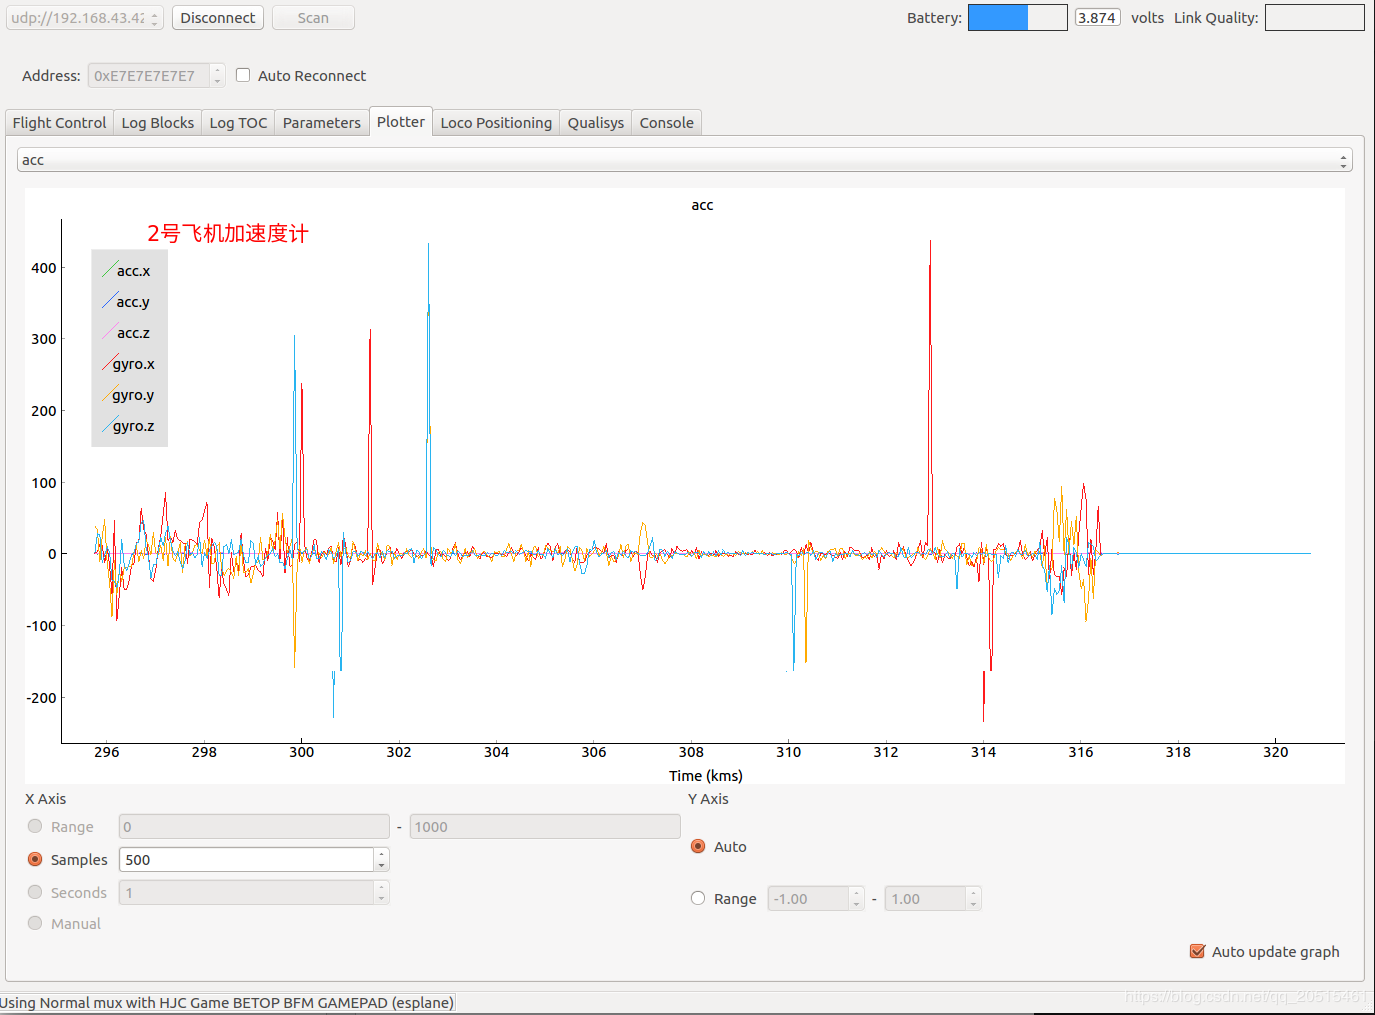
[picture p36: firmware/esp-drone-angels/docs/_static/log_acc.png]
accelerometer logging


   Accelerometer Logging

Propeller Direction
=======================

- Install A and B propellers according to the figure below.
- During the power-on self-test, check if the propellers spin properly.

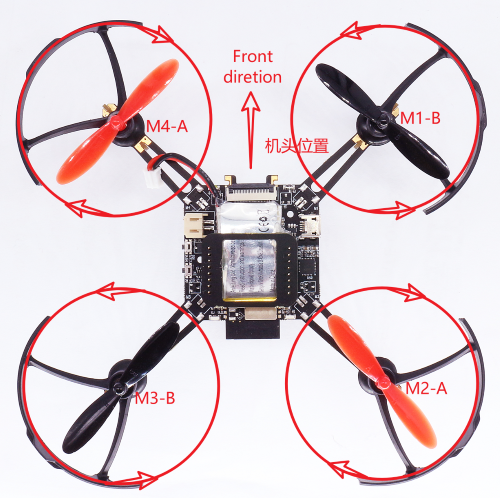
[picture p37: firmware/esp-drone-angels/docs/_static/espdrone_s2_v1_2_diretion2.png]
Propeller check


   Propeller Check

Preflight Check
================

- Place the drone with its head on the front, and its tail (i.e. the antenna part) at the back.
- Place the drone on a level surface and power it up when the drone stays still.
- Check on the cfclient if the drone is placed level.
- After the communication is established, check if the LED at the drone tail blinks GREEN fast.
- Check if the LED on the drone head blinks RED, which indicates battery LOW.
- Slide forward the Trust controller slightly at the left side of your APP (i.e. the commands controlled by your left finger), to check if the drone can respond the command quickly.
- Move your finger at the right command area of the APP (i.e. the commands controlled by your right finger), to check if the direction control works well.
- Go fly and have fun!

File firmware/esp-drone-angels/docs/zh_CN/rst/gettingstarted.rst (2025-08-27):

========
快速入门
========

:link_to_translation:`en:[English]`

项目简介
========

ESP-Drone 是基于乐鑫 ESP32/ESP32-S2/ESP32-S3 开发的小型无人机解决方案，可使用手机 APP 或游戏手柄通过 Wi-Fi
网络进行连接和控制。该方案硬件结构简单，代码架构清晰，支持功能扩展，可用于
STEAM 教育等领域。项目部分代码来自 Crazyflie 开源工程，继承 GPL3.0
开源协议。

ESP-Drone 无人机
   
   ESP-Drone 无人机

主要特性
---------

ESP-Drone 具备以下特性：

-  支持自稳定模式 (Stabilize mode)：自动控制机身水平，保持平稳飞行。
-  支持定高模式 (Height-hold mode)：自动控制油门输出，保持固定高度。
-  支持定点模式 (Position-hold mode)：自动控制机身角度，保持固定空间位置。
-  支持 PC 上位机调试：使用 cfclient 上位机进行静态/动态调试。
-  支持 APP 控制：使用手机 APP 通过 Wi-Fi 轻松控制。
-  支持游戏手柄 (gamepad) 控制：通过 cfclient 使用游戏手柄轻松控制。

主要组件
----------------

ESP-Drone 2.0 使用模块化的设计思路，由主控板和扩展板组成。

-  **主控制板**：搭载 ESP32-S2 模组和支持基础飞行的必要传感器，并提供硬件扩展接口。
-  **扩展板**：搭载扩展传感器，可对接主控制板的硬件扩展接口，支持高级飞行功能。

==== ========================= ========================= ================== ========================== ==============
序号 模块名                    主要元器件                功能               接口                       安装位置
==== ========================= ========================= ================== ========================== ==============
1    主控制板 - **ESP32-S2**   ESP32-S2-WROVER + MPU6050 基础飞行           提供 I2C SPI GPIO 扩展接口
2    扩展板 - **定点模块**     PMW3901 + VL53L1X         室内定点飞行       SPI + I2C                  底部，面向地面
3    扩展板 - **气压定高模块** MS5611 气压               气压定高           I2C 或 MPU6050 从机        顶部或底部
4    扩展板 - **指南针模块**   HMC5883 罗盘              无头模式等高级模式 I2C 或 MPU6050 从机        顶部或底部
==== ========================= ========================= ================== ========================== ==============

详情可查阅：`硬件参考 <./hardware.rst>`__。

ESP-IDF 简介
================

ESP-IDF 是乐鑫为 ESP32/ESP32-S2/ESP32-S3 提供的物联网开发框架。

-  ESP-IDF 包含一系列库及头文件，提供了基于 ESP32/ESP32-S2/ESP32-S3 构建软件项目所需的核心组件。
-  ESP-IDF 还提供了开发和量产过程中最常用的工具及功能，例如：构建、烧录、调试和测量等。

详情可查阅：`ESP-IDF 编程指南 <https://docs.espressif.com/projects/esp-idf/en/release-v5.0/esp32s2/get-started/index.html>`__。

Crazyflie 简介
================

Crazyflie 是来自 Bitcraze 开源工程的四旋翼飞行器，具备以下特性：

-  支持多种传感器组合，可以轻松实现定高模式、定点模式等高级飞行模式。
-  基于 FreeRTOS 编写，将复杂的无人机系统，分解成多个具有不同优先级的软件任务。
-  设计了功能完备的 cfclient 上位机和 CRTP 通信协议，便于实现调试、测量和控制。

crazyflie-overview

   多架无人机同时探索周围环境，灵活避开障碍物，同时避开其它无人机。\ `A
   swarm of drones exploring the environment, avoiding obstacles and
   each other. (Guus Schoonewille, TU
   Delft) <https://img-blog.csdnimg.cn/20191030202634944.jpg?x-oss-process=image/watermark,type_ZmFuZ3poZW5naGVpdGk,shadow_10,text_aHR0cHM6Ly9ibG9nLmNzZG4ubmV0L3FxXzIwNTE1NDYx,size_16,color_FFFFFF,t_70>`__

详情可查阅 `Crazyflie 官网 <https://www.bitcraze.io/>`__。

准备工作
================

硬件组装
----------

请按照下述步骤组装 ESP32-S2-Drone V1.2：

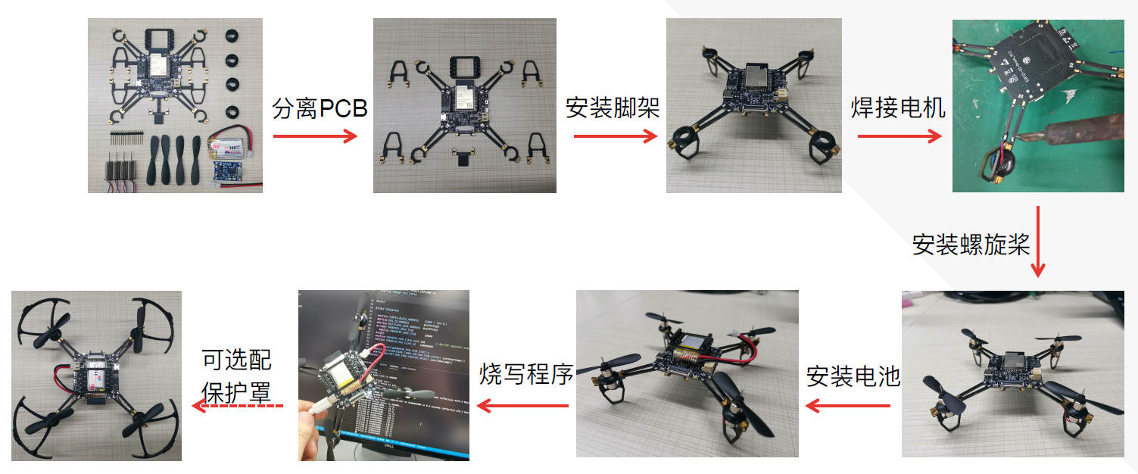
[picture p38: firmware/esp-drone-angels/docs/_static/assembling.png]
ESP32-S2-Drone V1.2 组装流程

   
   ESP32-S2-Drone V1.2 组装流程

硬件介绍和管脚资源分配可查阅：`硬件参考 <./hardware.rst>`__。

安装 ESP-Drone APP
--------------------

ESP-Drone APP 同时支持 Android 系统和 iOS 系统。

**扫描下方二维码，下载 Android APP：**

Android APP 扫码下载

**下载 iOS APP：**

在 App Store 中搜索 ESP-Drone，点击下载并安装。

**iOS APP 源代码**：`ESP-Drone-iOS <https://github.com/EspressifApps/ESP-Drone-iOS>`__

**Android APP 源代码**：`ESP-Drone-Android <https://github.com/EspressifApps/ESP-Drone-Android>`__

安装 cfclient
--------------------

安装 cfclient 为可选步骤，用于实现高级调试，非必须使用。

cfclient 上位机界面

   cfclient 上位机界面

**1. 安装 cfclient**

1.1 下载源代码

.. code:: text

   git clone https://github.com/qljz1993/crazyflie-clients-python.git

1.2 进入下载目录

.. code:: text

   cd crazyflie-clients-python

1.3 安装 cfclient 客户端

.. code:: text

   pip3 install -e .

1.4 启动客户端

.. code:: text

   cfclient

**2. 配置遥控器**

游戏手柄配置

   遥控器配置

2.1 配置 4 个控制轴：``Roll 、Pitch、Yaw、Thrust``。

2.2 配置一个按键为 ``Assisted control``，用于飞行模式切换。

手机 APP 使用指南
========================

Wi-Fi 连接
---------------------------
* 手机扫描 Wi-Fi AP。ESP-Drone 设备用作 AP，其 SSID 及密码如下：

::

   SSID：ESP-DRONE_XXXX（XXXX 根据 MAC 设置）PASSWORD：12345678

* 点击该 AP，手机与 ESP-Drone 设备建立 Wi-Fi 连接。

个性化设置
-----------

在该步骤中，您可以按照具体的应用场景进行个性化配置，或使用默认配置。

::

   ```
   默认配置：

   Flight control settings 
       1. Mode: Mode2
       2. Deadzone: 0.2
       3. Roll trim: 0.0
       4. Pitch trim: 0.0
       5. Advanced flight control : true
       6. Advanced flight control preferences 
           1. max roll/pitch angle: 15
           2. max yaw angle: 90
           3. max thrust: 90
           4. min thrust: 25
           5. X-Mode: true
   Controller settings 
       1. use full travel for thrust: false
       2. virtual joystick size: 100
   App settings
       1. Screen rotation lock: true
       2. full screen mode:true
       3. show console: true   
   ```

控制飞行
--------

-  打开 APP，点击 `Connect` 按钮，连接小飞机。连接成功，小飞机绿灯闪烁。
-  轻推油门，小飞机起飞。
-  在 APP 上滑动，控制小飞机方向。

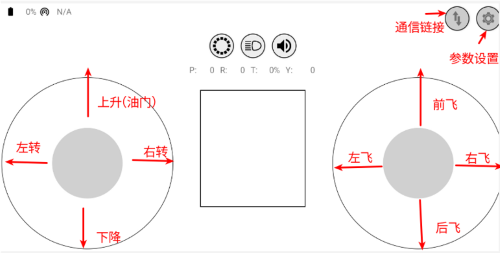
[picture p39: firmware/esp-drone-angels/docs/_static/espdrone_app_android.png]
Android APP 用户界面


   Android APP 用户界面

PC cfclient 使用指南
========================

cfclient 是 ``Crazeflie`` 源工程的上位机，完全实现了 ``CRTP``
协议中定义的功能，可以加快飞机的调试过程。ESP-Drone
项目对该上位机进行裁剪和调整，满足功能设计需求。

cfclient 架构

   cfclient 架构

cfclient 控制台界面

   cfclient 控制台界面

项目中有很多相关的文件，例如配置文件和缓存文件，其中 JSON
文件用来存储配置信息。关于配置信息中内容的解读，可参考：`User
Configuration
File <https://www.bitcraze.io/documentation/repository/crazyflie-clients-python/master/development/dev_info_client/>`__。

飞行设置
----------

基本飞行设置 (Basic Flight Control)
~~~~~~~~~~~~~~~~~~~~~~~~~~~~~~~~~~~~~

1. 飞行模式 (Flight mode)：基本模式和高级模式

   -  基本模式 (Normal mode)：初学者使用。
   -  高级模式 (Advanced mode)：设置解锁最大角度，设置最大油门。

2. 自动模式 (Assisted mode)

   -  定海拔模式 (Altitude-hold mode)：保持飞行海拔，需要气压计支持。
   -  定点模式 (Position-hold mode)：保持当前位置，需要光流和 TOF 支持。
   -  定高模式 (Height-hold mode)：保持相对高度，触发时保持高于地面 40
      cm，需要 TOF 支持。
   -  悬停模式 (Hover mode)：触发时保持高于地面 40
      cm，并悬停在起飞点，需要光流和 TOF 支持。

3. 角度修正 (Trim)

   -  翻滚角修正 (Roll Trim)：用于弥补传感器水平安装误差。
   -  俯仰角修正 (Pitch Trim)：用于弥补传感器水平安装误差。

注意，在自动模式下，油门摇杆变为高度控制摇杆。

高级飞行设置 (Advanced Flight Control)
~~~~~~~~~~~~~~~~~~~~~~~~~~~~~~~~~~~~~~

1. 最大倾角 (Max angle)：设置最大允许的俯仰和翻滚角度：roll/pitch。
2. 最大自旋速度 (Max yaw rate)：设置允许的偏航速度：yaw。
3. 最大油门 (Max thrust)：设置最大油门。
4. 最小油门 (Min thrust)：设置最小油门。
5. 压摆极限 (Slew limit)：防止油门骤降，油门低于该值时，下降速度将被限定。
6. 压摆率 (Slew rate)：油门到压摆极限之后的最大下降率。

遥控器设置 (Configure Input Device)
~~~~~~~~~~~~~~~~~~~~~~~~~~~~~~~~~~~~~~

按照提示绑定遥控器摇杆与各个控制通道：

cfclient 控制器配置

飞行数据 (Flight Data)
~~~~~~~~~~~~~~~~~~~~~~~~~~

驾驶仪可以看到当前飞机姿态，右下方显示对应的详细数据。

1. 目标角度 (Target)
2. 测量角度 (Actual)
3. 当前油门值 (Thrust)
4. 电机实际输出 (M1/M2/M3/M4)

在线参数修改
--------------------

**在线调整 PID 参数**

PID 参数调整
   
   cfclient PID 参数调整

**注意事项**

1. 修改的参数实时生效，避免了频繁烧录固件。
2. 可在代码中通过宏定义，配置哪些参数可被上位机实时修改。
3. 注意，参数在线修改仅用于调试，掉电不保存。

飞行数据监控
--------------------

**配置要监控的参数**

PID 参数调整

   监控参数配置

PID 参数调整

   参数配置区

**实时波形绘制**

陀螺仪加速度计实时数据监测：

PID 参数调整

   陀螺仪加速度计数据监测

螺旋桨方向
================

-  按照下图所示位置，安装 A、B 螺旋桨。
-  飞行器上电自检时，检查螺旋桨转向是否正确。

螺旋桨方向示图

   螺旋桨方向示图

起飞前检查
================

-  将小飞机头部朝前放置，尾部天线朝向自己；
-  将小飞机置于水平面上，待机身稳定时上电；
-  观察上位机水平面是否置平；
-  观察通信建立以后，小飞机尾部绿灯是否快速闪烁；
-  观察小飞机头部红灯是否熄灭，亮起代表电量不足；
-  轻推左手小油门，检查飞机是否能快速响应；
-  轻推右手方向，检查方向控制是否正确；
-  起飞吧！

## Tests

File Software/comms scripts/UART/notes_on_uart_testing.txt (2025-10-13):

Notes on UART testing

1. Configure the serial hardware to be enabled:

	"""
	sudo raspi-config
	# Interface Options → Serial
	#   Login shell over serial?  → No
	#   Enable serial hardware?   → Yes
	sudo reboot
	"""

1. Edit /boot/config.txt with:

	"""
	cd ..
	cd ..
	cd boot
	cd firmware
	sudo nano config.txt
	#	change "dtoverlay=vc4-kms-v3d" to "dtoverlay=disable-bt"
	#	add "init_uart_clock=48000000"	
	#	CTRL+O, ENTER to save
	#	CTRL+X to exit
	"""
		
1. Run this:
	
	"""
	sudo systemctl disable hciuart.service
	sudo reboot
	"""
	
1. Check with this:

	""" 
	ls -l /dev/serial*
	# 	Should see '... /dev/serial0 -> ttyAMA0'
	""" 
	
1. Install pyserial in a venv with:

	"""
	cd ~
	python3 -m venv venv-serial
	source ~/venv-serial/bin/activate
	python -m pip install --upgrade pip
	pip install pyserial
	"""
	
1. Check UART frames are being sent with:

	""" 
	python -m serial.tools.miniterm /dev/serial0 921600 --raw | hexdump -C
	#	CTRL+C to stop
	"""
	
1. On ground station (with both on hotspot), navigate to sniffer.py and copy to Pi with:

	"""
	scp sniffer.py erwin@raspberrypi.local:/home/erwin/
	#	Enter password: 12345678
	#	Obvs change to match your device
	"""

1. Run on Pi with:

	"""
	sudo systemctl disable --now serial-getty@ttyAMA0.service serial-getty@ttyS0.service hciuart
	sudo chrt -f 80 ionice -c1 nice -n -20 /home/erwin/imu-venv/bin/python /home/erwin/sniffer.py --throttle 50
	#	Remove --throttle 50 if you want everything to print
	#	Change file paths to match your device
	"""

1. On the ground station, prepare for drone discovery test with:

	"""
	cd ~/Projects/drone-project/comms\ scripts/UART
	python3 -m venv venv-uart
	source venv-uart/bin/activate
	python3 -m pip install --upgrade pip
	pip install scapy netifaces
	"""

1. Run drone discovery test with:

	"""
	sudo ./venv-uart/bin/python3 discovery.py
	"""

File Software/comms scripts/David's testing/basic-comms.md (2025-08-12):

# Network scan for ip

sudo nmap your_ip/your_subnet

# test video steaming  pi -> groundstation 

ffmpeg -re -f lavfi -i testsrc=size=640x480:rate=30 -c:v libx264 -f mpegts udp://<GCS_IP>:5000

# on ground station

ffplay udp://@:5000

ffplay -fflags nobuffer -flags low_delay -i udp://0.0.0.0:5004

gst-launch-1.0 -v udpsrc port=5004 \
  caps="application/x-rtp, media=video, encoding-name=H264, payload=96" \
  ! rtph264depay ! h264parse ! avdec_h264 \
  ! videoconvert ! autovideosink sync=false

# Basic iperf3 stress test on GS run first

iperf3 -s

# Then on the pi run

iperf3 -c <GCS_IP> -u -b 10M

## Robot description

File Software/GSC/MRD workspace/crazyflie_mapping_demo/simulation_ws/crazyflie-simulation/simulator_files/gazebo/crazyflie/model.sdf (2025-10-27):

<?xml version="1.0" ?>
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

<sdf version="1.8">
  <model name="crazyflie">
    <link name="crazyflie/body">
      <pose> 0 0 17.425E-3 0 0 0</pose>
      <inertial>
        <mass>0.025</mass>
        <inertia>
          <ixx>16.571710E-06</ixx>
          <iyy>16.655602E-06</iyy>
          <izz>29.261652E-06</izz>
          <ixy>0.830806E-06</ixy>
          <ixz>0.718277E-06</ixz>
          <iyz>1.800197E-06</iyz>
        </inertia>
      </inertial>
      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
      <sensor name='range_up' type='gpu_lidar'>
        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
        <pose relative_to='crazyflie/base_link'>0 0 0.15 0 -1.5708 0</pose>
        <update_rate>30</update_rate>
        <ray>
          <scan>
            <horizontal>
              <samples>1</samples>
              <resolution>1</resolution>
              <min_angle>0</min_angle>
              <max_angle>0</max_angle>
            </horizontal>
            <vertical>
              <samples>1</samples>
              <resolution>1</resolution>
              <min_angle>0</min_angle>
              <max_angle>0</max_angle>
            </vertical>
          </scan>
          <range>
            <min>0.01</min>
            <max>3.49</max>
            <resolution>0.01</resolution>
          </range>
        </ray>
        <always_on>1</always_on>
        <visualize>true</visualize>
        <topic>range_up_scan</topic>
      </sensor>

      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
      <sensor name='range_down' type='gpu_lidar'>
        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
        <pose relative_to='crazyflie/base_link'>0 0 -0.15 0 1.5708 0</pose>
        <update_rate>30</update_rate>
        <ray>
          <scan>
            <horizontal>
              <samples>1</samples>
              <resolution>1</resolution>
              <min_angle>0</min_angle>
              <max_angle>0</max_angle>
            </horizontal>
            <vertical>
              <samples>1</samples>
              <resolution>1</resolution>
              <min_angle>0</min_angle>
              <max_angle>0</max_angle>
            </vertical>
          </scan>
          <range>
            <min>0.01</min>
            <max>3.49</max>
            <resolution>0.01</resolution>
          </range>
        </ray>
        <always_on>1</always_on>
        <visualize>true</visualize>
        <topic>range_down_scan</topic>
      </sensor>

      <sensor name='multiranger' type='gpu_lidar'>
        <pose relative_to='crazyflie/base_link'>0 0 0.1 0 0 0</pose>
        <topic>lidar</topic>
        <update_rate>60</update_rate>
        <ray>
          <scan>
            <horizontal>
                <samples>4</samples>
                <resolution>1</resolution>
                <min_angle>-3.14</min_angle>
                <max_angle>1.57</max_angle>
            </horizontal>
            <vertical>
                <samples>1</samples>
                <resolution>0.01</resolution>
                <min_angle>0</min_angle>
                <max_angle>0</max_angle>
            </vertical>
          </scan>
          <range>
            <min>0.01</min>
            <max>3.49</max>
            <resolution>0.01</resolution>
          </range>
        </ray>
        <always_on>1</always_on>
        <visualize>true</visualize>
      </sensor>
    </link>
    <link name="crazyflie/m1_prop">
      <pose>0.031 -0.031 0.021 0 0 0</pose>
      <inertial>
        <mass>0.0008</mass>
        <inertia>
          <ixx>8.33333E-09</ixx>
          <iyy>1.08333E-07</iyy>
          <izz>1.13333E-07</izz>
        </inertia>
      </inertial>
      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
    </link>
    <link name="crazyflie/m2_prop">
      <pose>-0.031 -0.031 0.021 0 0 0</pose>
      <inertial>
        <mass>0.0008</mass>
        <inertia>
          <ixx>8.33333E-09</ixx>
          <iyy>1.08333E-07</iyy>
          <izz>1.13333E-07</izz>
        </inertia>
      </inertial>
      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
    </link>
    <link name="crazyflie/m3_prop">
      <pose>-0.031 0.031 0.021 0 0 0</pose>
      <inertial>
        <mass>0.0008</mass>
        <inertia>
          <ixx>8.33333E-09</ixx>
          <iyy>1.08333E-07</iyy>
          <izz>1.13333E-07</izz>
        </inertia>
      </inertial>
      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
    </link>
    <link name="crazyflie/m4_prop">
      <pose>0.031 0.031 0.021 0 0 0</pose>
      <inertial>
        <mass>0.0008</mass>
        <inertia>
          <ixx>8.33333E-09</ixx>
          <iyy>1.08333E-07</iyy>
          <izz>1.13333E-07</izz>
        </inertia>
      </inertial>
      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
    </link>
    <joint name="crazyflie/m1_joint" type="revolute">
      <child>crazyflie/m1_prop</child>
      <parent>crazyflie/body</parent>
      <axis>
        <xyz>0 0 1</xyz>
      </axis>
    </joint>
    <joint name="crazyflie/m2_joint" type="revolute">
      <child>crazyflie/m2_prop</child>
      <parent>crazyflie/body</parent>
      <axis>
        <xyz>0 0 1</xyz>
      </axis>
    </joint>
    <joint name="crazyflie/m3_joint" type="revolute">
      <child>crazyflie/m3_prop</child>
      <parent>crazyflie/body</parent>
      <axis>
        <xyz>0 0 1</xyz>
      </axis>
    </joint>
    <joint name="crazyflie/m4_joint" type="revolute">
      <child>crazyflie/m4_prop</child>
      <parent>crazyflie/body</parent>
      <axis>
        <xyz>0 0 1</xyz>
      </axis>
    </joint>
    <plugin filename="gz-sim-multicopter-motor-model-system" name="gz::sim::systems::MulticopterMotorModel">
      <robotNamespace>crazyflie</robotNamespace>
      <jointName>crazyflie/m1_joint</jointName>
      <linkName>crazyflie/m1_prop</linkName>
      <turningDirection>ccw</turningDirection>
      <maxRotVelocity>2618</maxRotVelocity>
      <motorConstant>1.28192e-08</motorConstant>
      <momentConstant>0.005964552</momentConstant>
      <rotorDragCoefficient>2.0e-05</rotorDragCoefficient>
      <rollingMomentCoefficient>0.0000001</rollingMomentCoefficient>
      <rotorVelocitySlowdownSim>20</rotorVelocitySlowdownSim>
      <actuator_number>0</actuator_number>
      <motorType>velocity</motorType>
    </plugin>
    <plugin filename="gz-sim-multicopter-motor-model-system" name="gz::sim::systems::MulticopterMotorModel">
      <robotNamespace>crazyflie</robotNamespace>
      <jointName>crazyflie/m2_joint</jointName>
      <linkName>crazyflie/m2_prop</linkName>
      <turningDirection>cw</turningDirection>
      <maxRotVelocity>2618</maxRotVelocity>
      <motorConstant>1.28192e-08</motorConstant>
      <momentConstant>0.005964552</momentConstant>
      <rotorDragCoefficient>2.0e-05</rotorDragCoefficient>
      <rollingMomentCoefficient>0.0000001</rollingMomentCoefficient>
      <rotorVelocitySlowdownSim>20</rotorVelocitySlowdownSim>
      <actuator_number>1</actuator_number>
      <motorType>velocity</motorType>
    </plugin>
    <plugin filename="gz-sim-multicopter-motor-model-system" name="gz::sim::systems::MulticopterMotorModel">
      <robotNamespace>crazyflie</robotNamespace>
      <jointName>crazyflie/m3_joint</jointName>
      <linkName>crazyflie/m3_prop</linkName>
      <turningDirection>ccw</turningDirection>
      <maxRotVelocity>2618</maxRotVelocity>
      <motorConstant>1.28192e-08</motorConstant>
      <momentConstant>0.005964552</momentConstant>
      <rotorDragCoefficient>2.0e-05</rotorDragCoefficient>
      <rollingMomentCoefficient>0.0000001</rollingMomentCoefficient>
      <rotorVelocitySlowdownSim>20</rotorVelocitySlowdownSim>
      <actuator_number>2</actuator_number>
      <motorType>velocity</motorType>
    </plugin>
    <plugin filename="gz-sim-multicopter-motor-model-system" name="gz::sim::systems::MulticopterMotorModel">
      <robotNamespace>crazyflie</robotNamespace>
      <jointName>crazyflie/m4_joint</jointName>
      <linkName>crazyflie/m4_prop</linkName>
      <turningDirection>cw</turningDirection>
      <maxRotVelocity>2618</maxRotVelocity>
      <motorConstant>1.28192e-08</motorConstant>
      <momentConstant>0.005964552</momentConstant>
      <rotorDragCoefficient>2.0e-05</rotorDragCoefficient>
      <rollingMomentCoefficient>0.0000001</rollingMomentCoefficient>
      <rotorVelocitySlowdownSim>20</rotorVelocitySlowdownSim>
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

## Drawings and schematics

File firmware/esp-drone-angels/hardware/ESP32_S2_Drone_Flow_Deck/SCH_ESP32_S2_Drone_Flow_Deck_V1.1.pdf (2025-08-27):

## Connectors

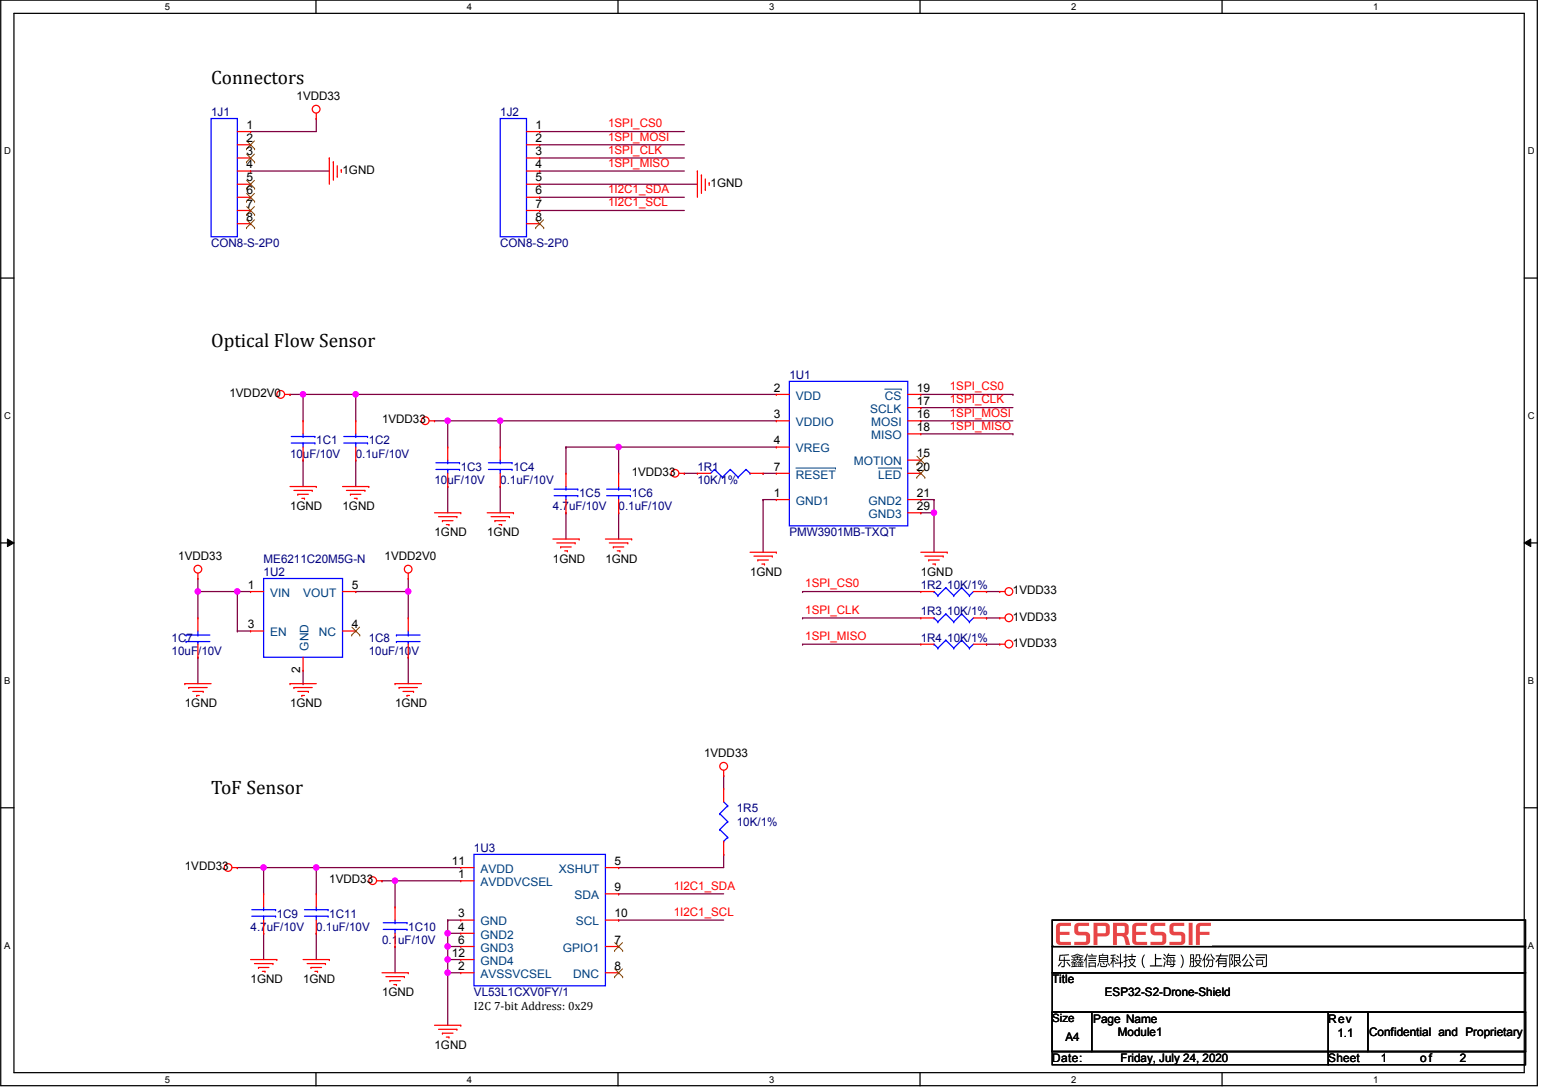
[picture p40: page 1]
I2C 7-bit Address: 0x29; ToF Sensor; 1SPI_CLK; 1SPI_MOSI; 1SPI_CS0; 1SPI_MISO; 1I2C1_SDA 1I2C1_SCL; 1I2C1_SDA; 1I2C1_SCL; 1VDD33; 1GND; 1VDD2V0; Title; Size; Page Name; Rev; Date:; Sheet; ESP32-S2-Drone-Shield; Friday, July 24, 2020; Module1; VL53L1CXV0FY/1; AVDDVCSEL 1; AVSSVCSEL 2; GND 3 GND2 4; XSHUT; GND3 6; DNC; SDA; SCL; AVDD 11; GND4 12; GPIO1; CON8-S-2P0; PMW3901MB-TXQT; GND1 1; VDD 2; VDDIO 3; VREG 4; RESET 7; MOTION; MOSI; 16 SCLK; MISO; LED; GND3; 29 GND2; VIN 1; GND; VOUT

Optical Flow Sensor

Confidential and Proprietary

## Connectors

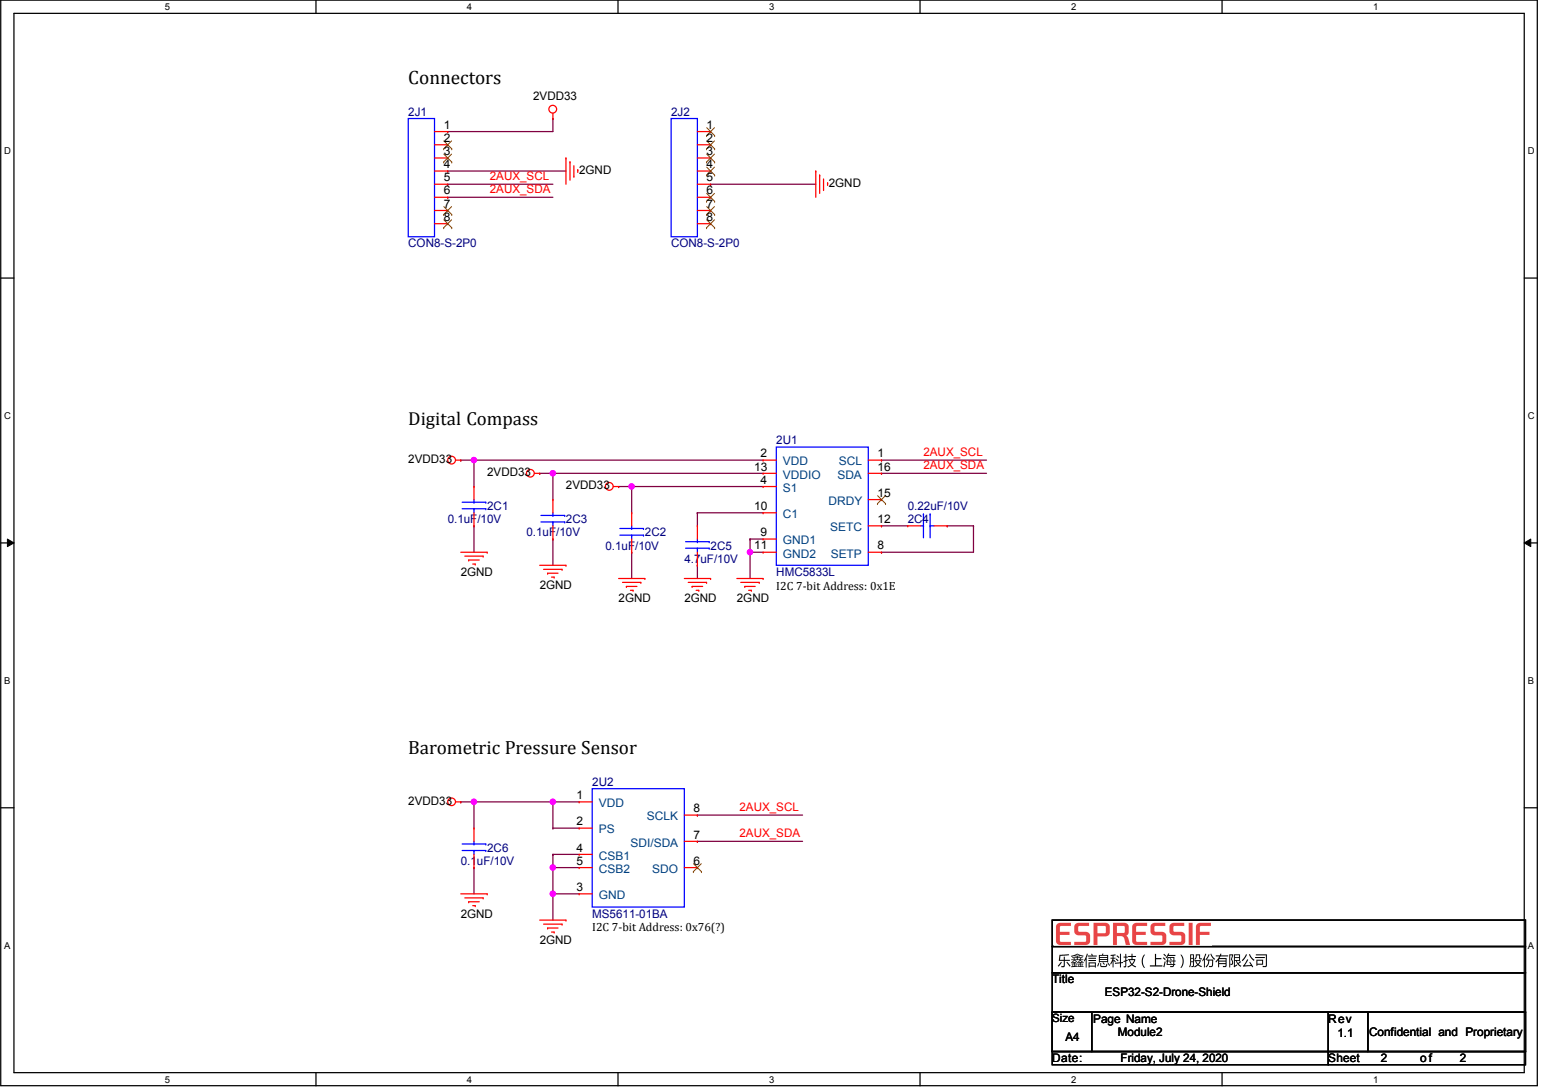
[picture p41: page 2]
Digital Compass; I2C 7-bit Address: 0x1E; I2C 7-bit Address: 0x76(?); 2AUX_SCL 2AUX_SDA; 2AUX_SCL; 2AUX_SDA; 2VDD33; 2GND; Title; Size; Page Name; Rev; Date:; Sheet; ESP32-S2-Drone-Shield; Friday, July 24, 2020; Module2; CON8-S-2P0; VDD 1; GND 3; CSB1 4; CSB2 5; SDO; SDI/SDA; SCLK; HMC5833L; SCL; 1 VDD 2; SETP; 8 GND1 9; GND2 11; SETC; VDDIO 13; DRDY; SDA

Barometric Pressure Sensor

Confidential and Proprietary

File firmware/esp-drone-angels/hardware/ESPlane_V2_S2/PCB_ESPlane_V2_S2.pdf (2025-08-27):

45.0mm

J2J2x1 | J2x2 | J2x3 | J2x4 | J2x5 | J2x6 | J2x7 | J2x8 | J2x9 | J2x10 | J2x11 | J2x12 | J2x13 | J2x14 | J2x15 | J2x16 | J2x17 | J2x18 | J2x19 | J2x20 | J2x21 | J2x22 | J2x23 | J2x24 J2x26 | J2x25

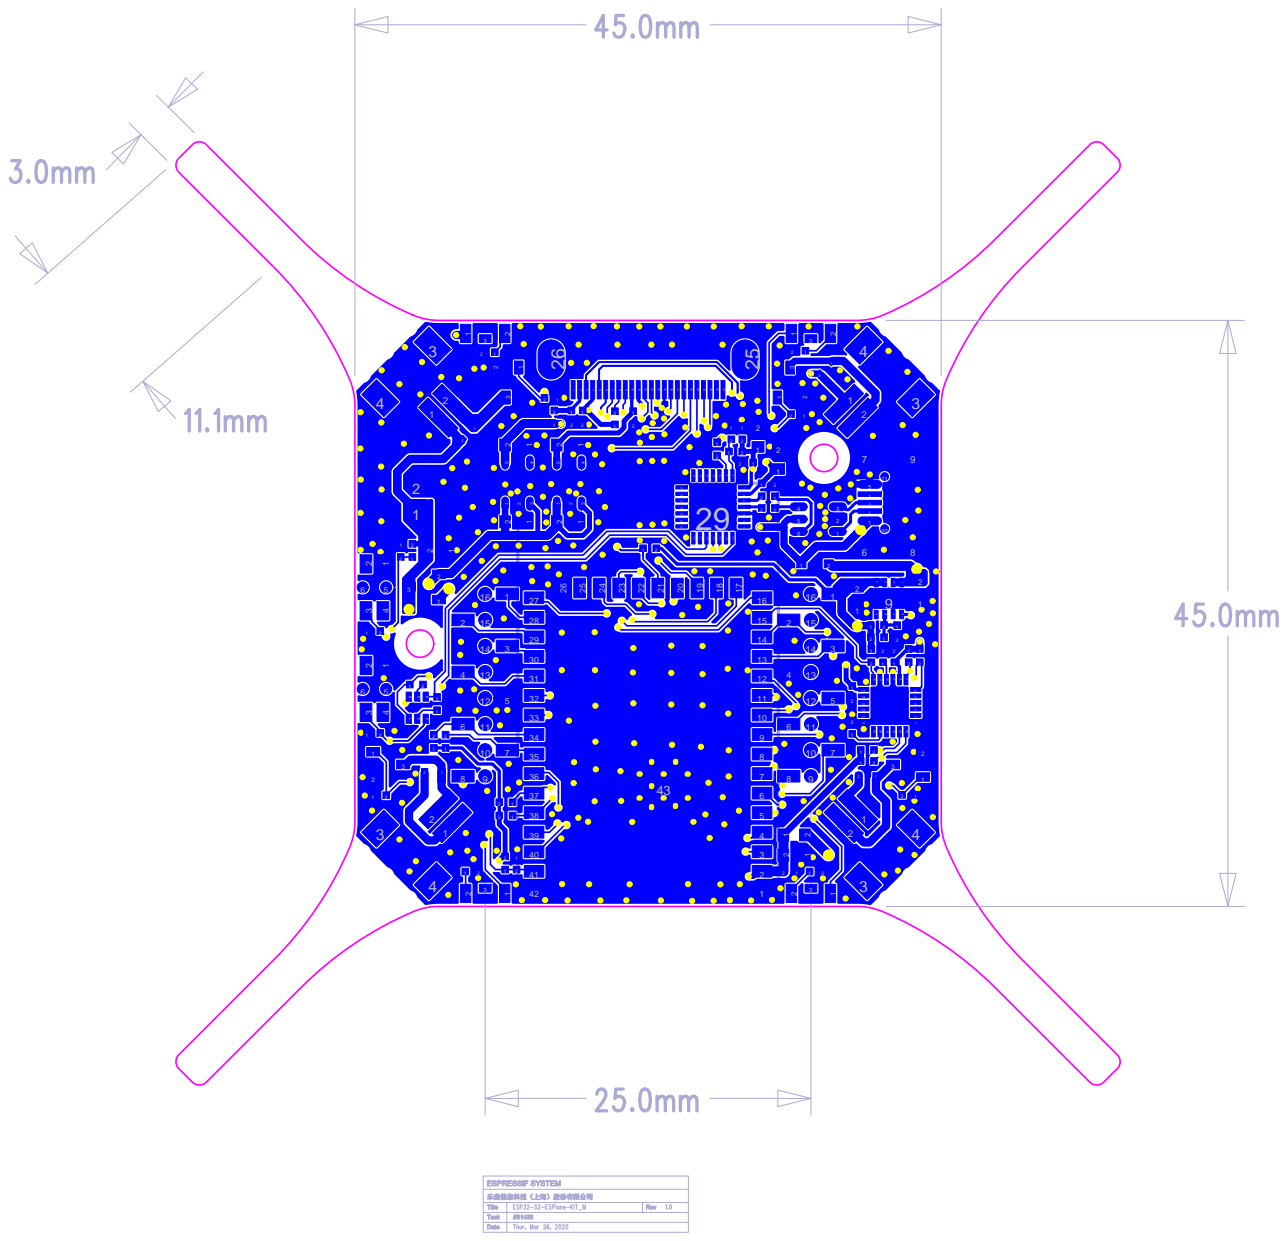
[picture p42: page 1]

45.0mm

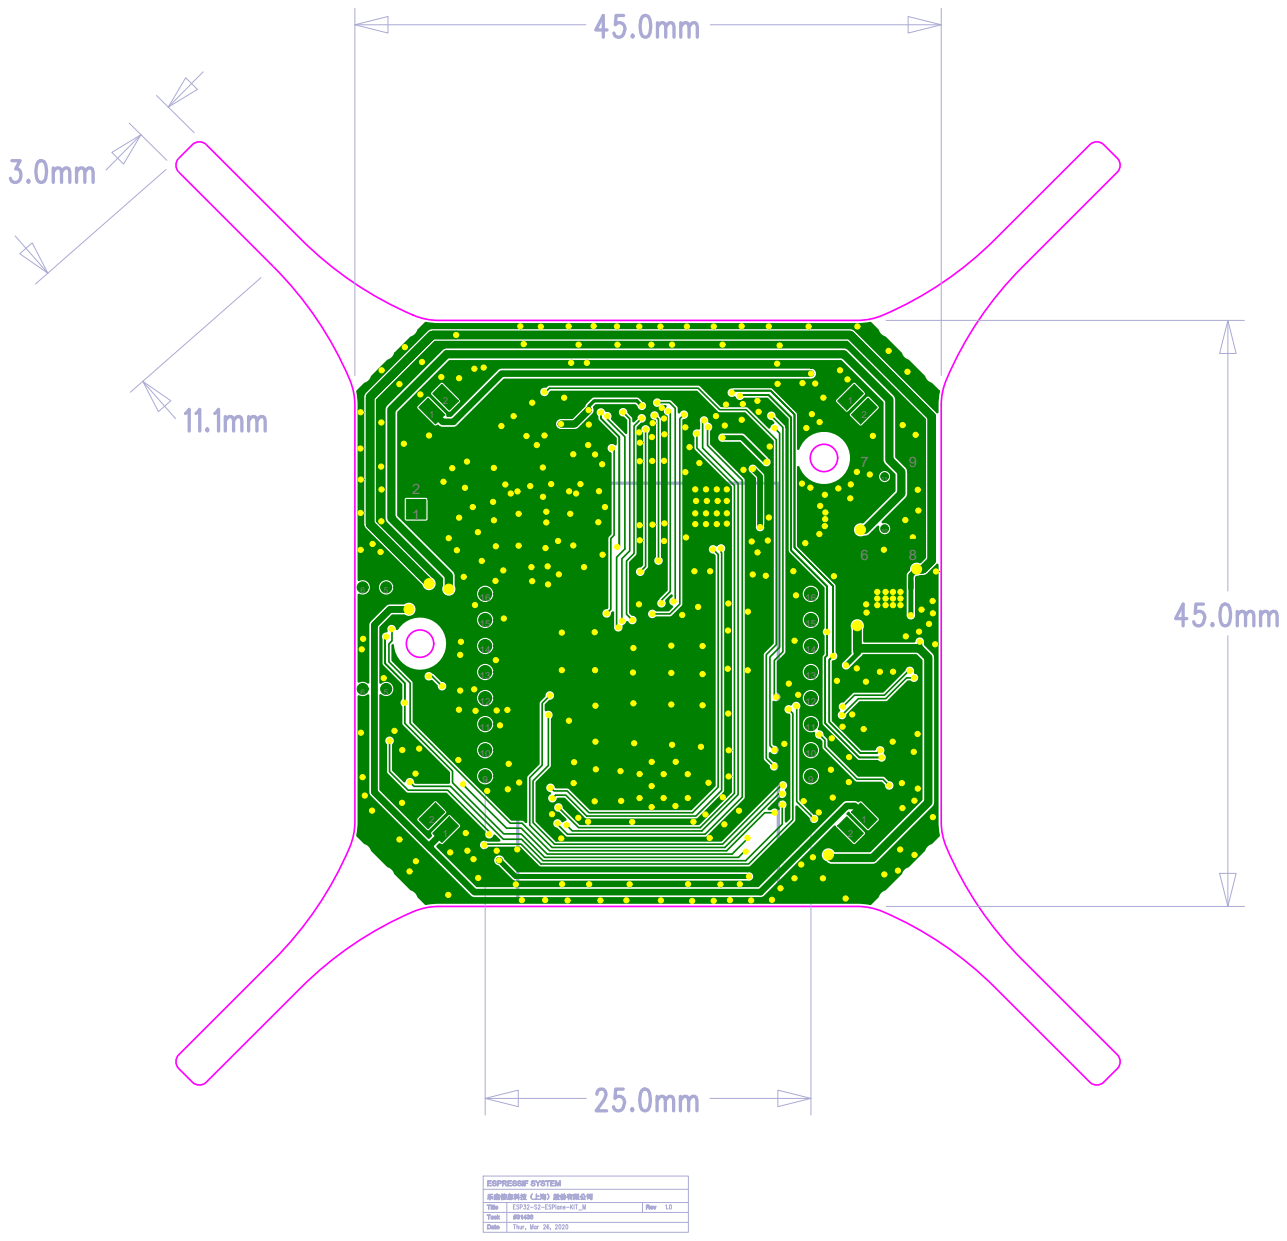
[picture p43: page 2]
Title; ESP32-S2-ESPlane-KIT_M; ESPRESSIF SYSTEM; Task; Date; Thur, Mar 26, 2020; Rev; SW1 SW¹x6; SW¹x5; SW2 SW²x6; SW²x5

乐鑫信息科技（上海）股份有限公司

45.0mm
J2

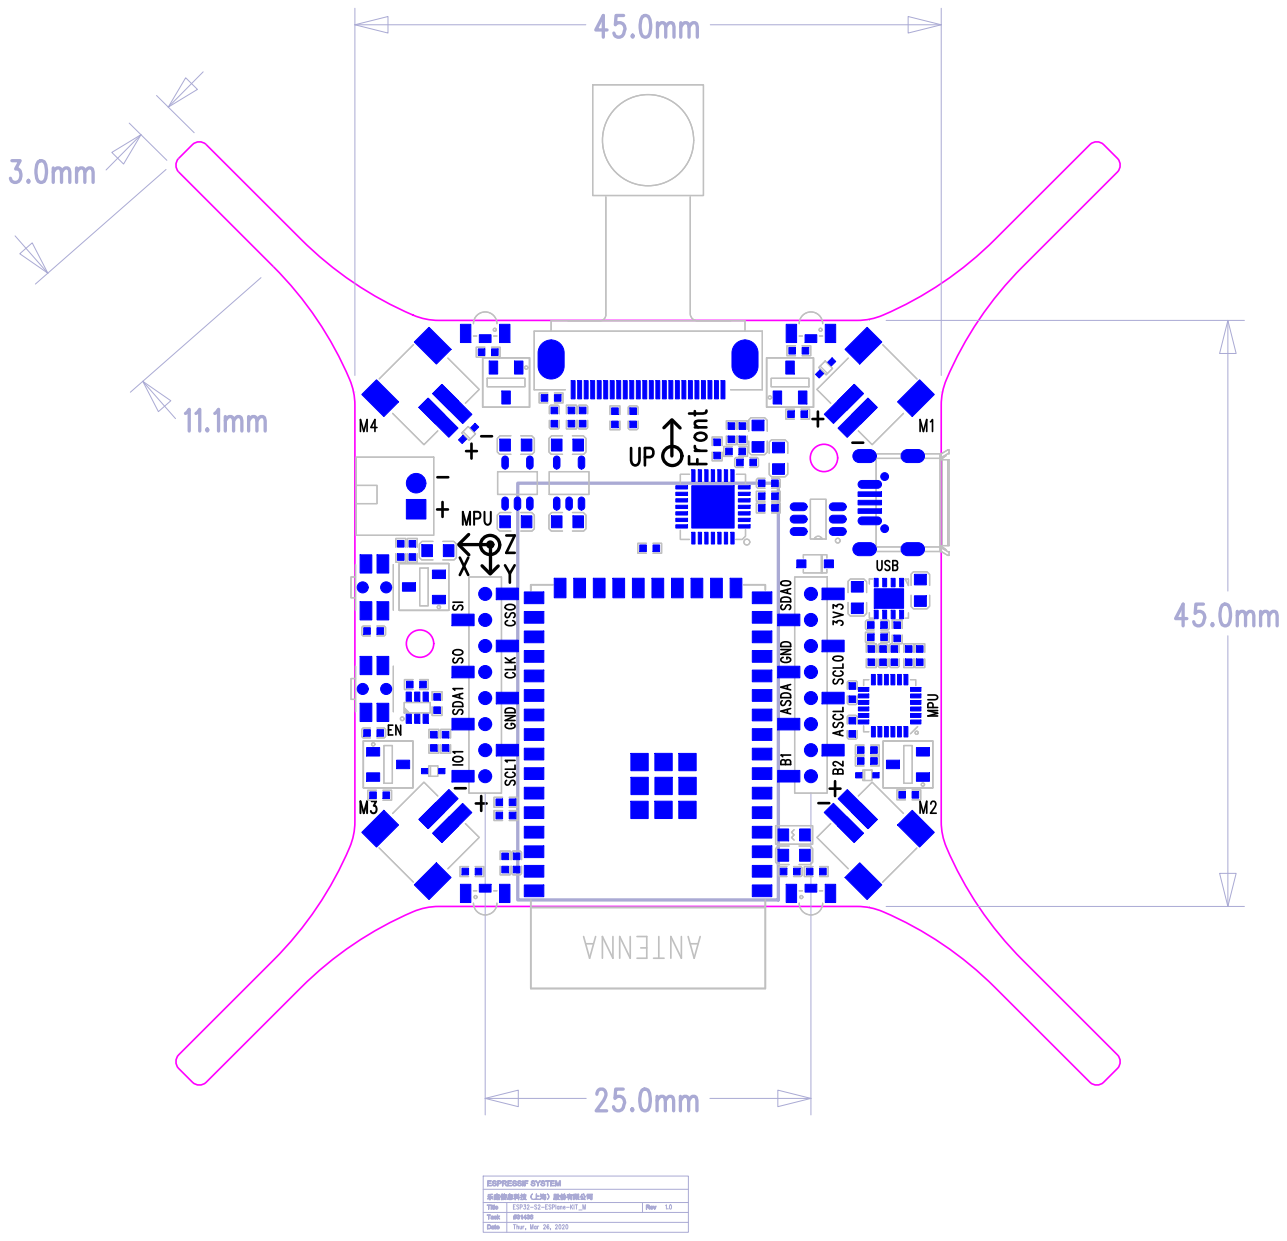
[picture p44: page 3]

45.0mm

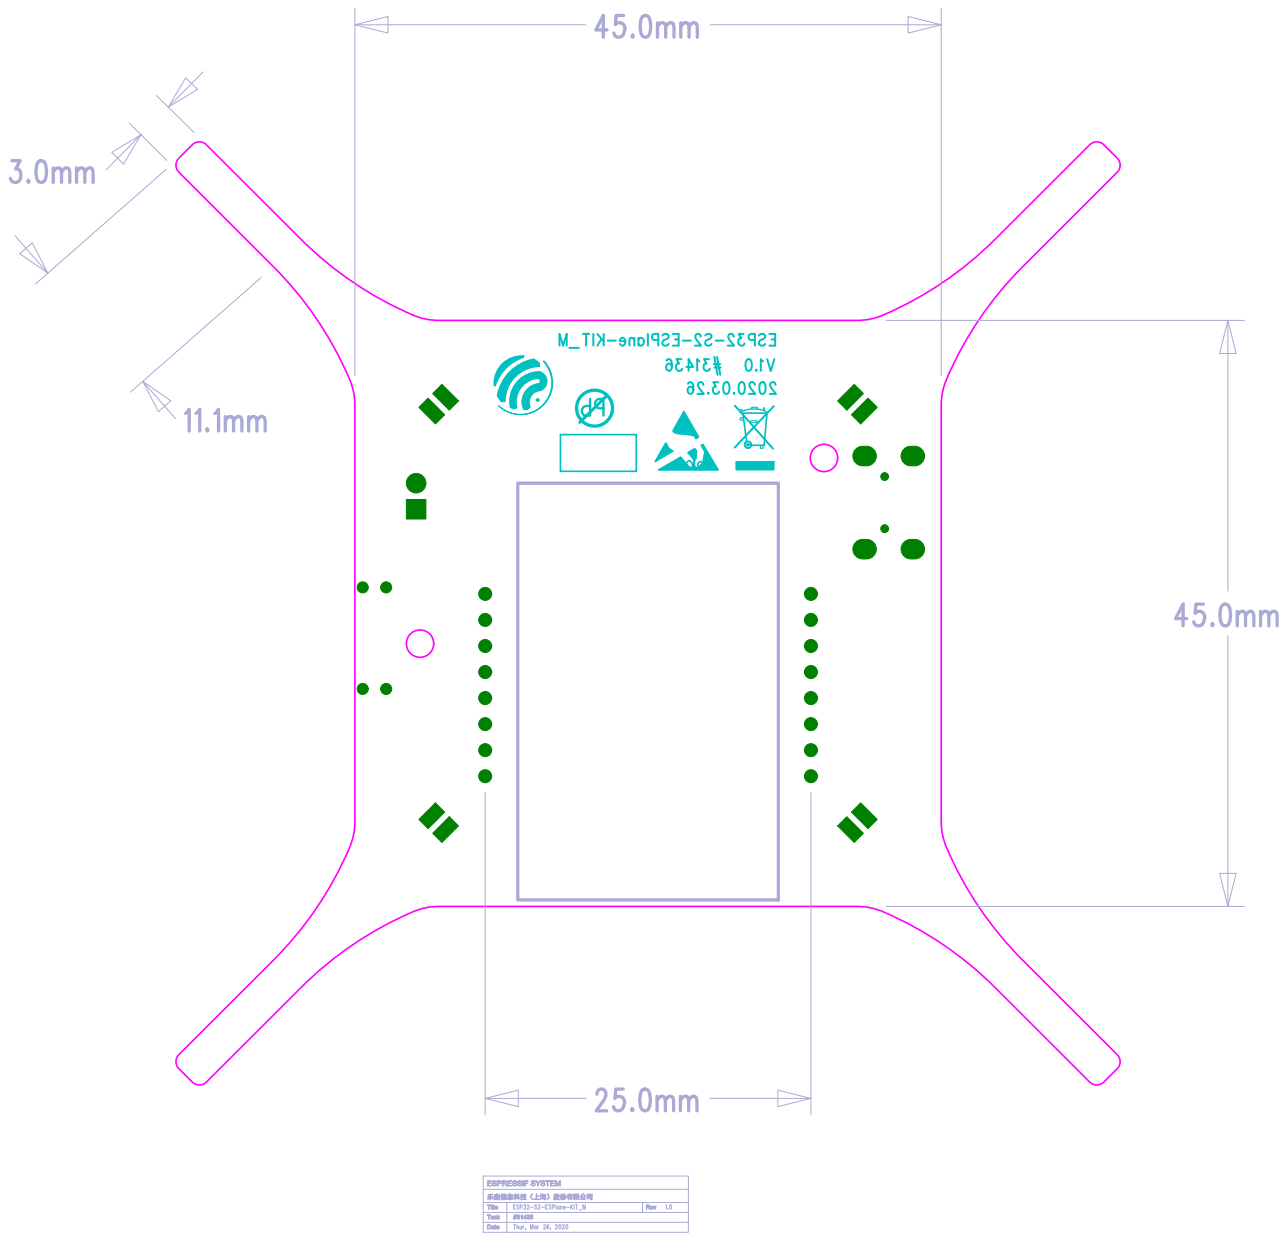
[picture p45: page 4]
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

乐鑫信息科技（上海）股份有限公司

45.0mm
J2

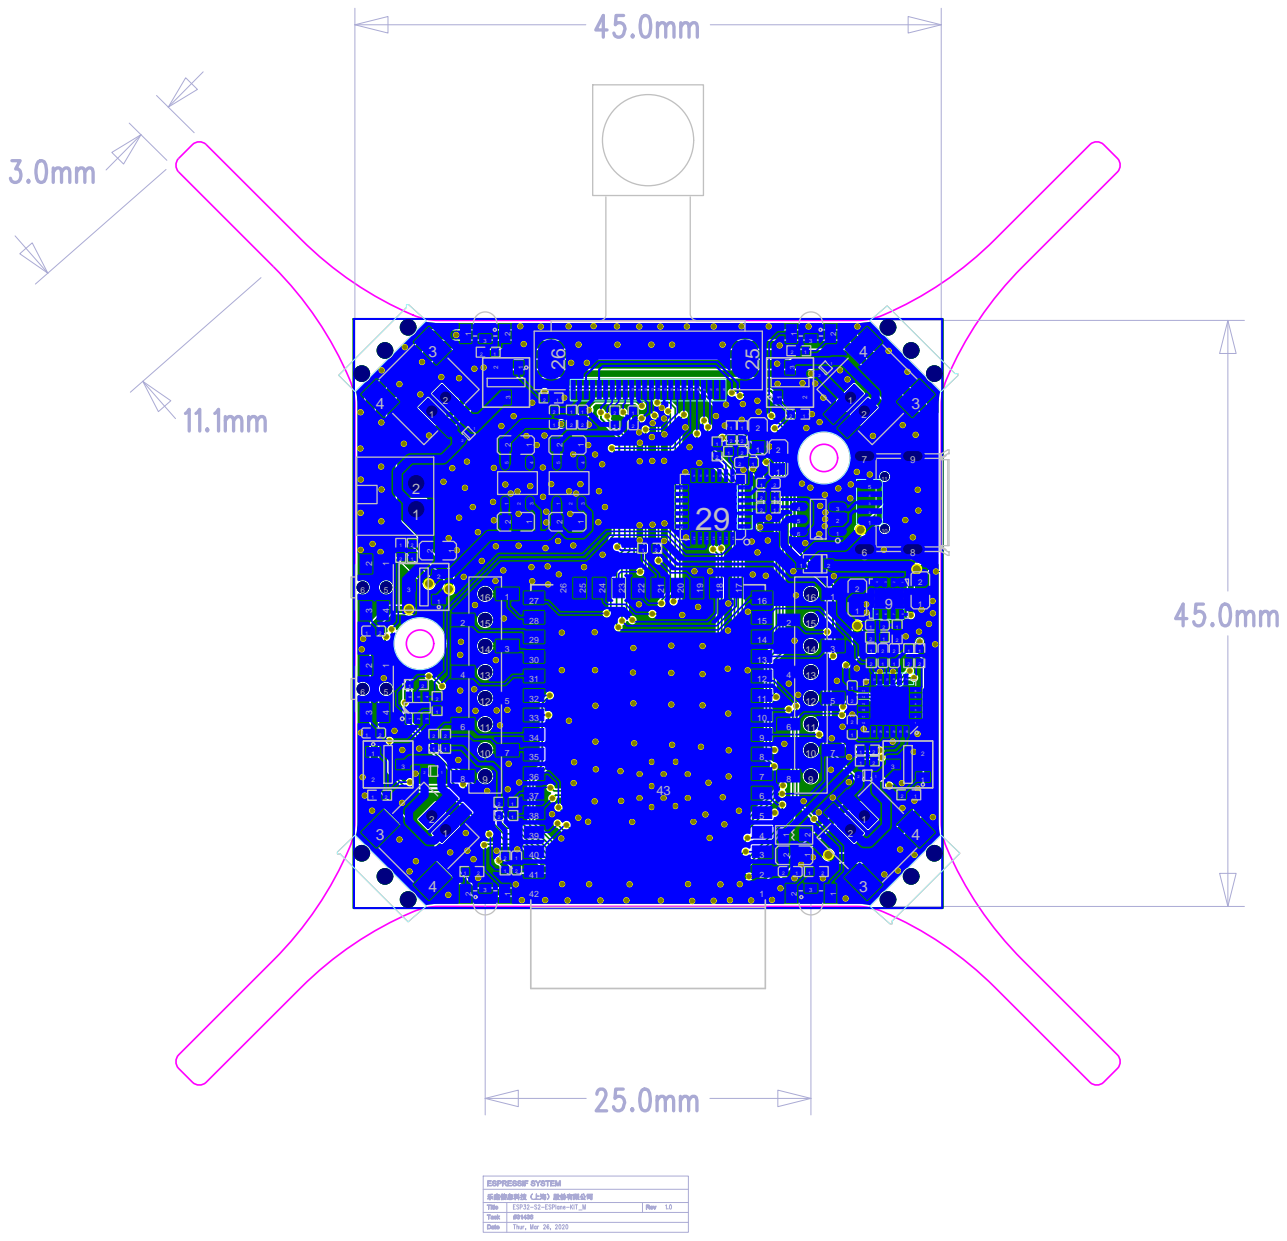
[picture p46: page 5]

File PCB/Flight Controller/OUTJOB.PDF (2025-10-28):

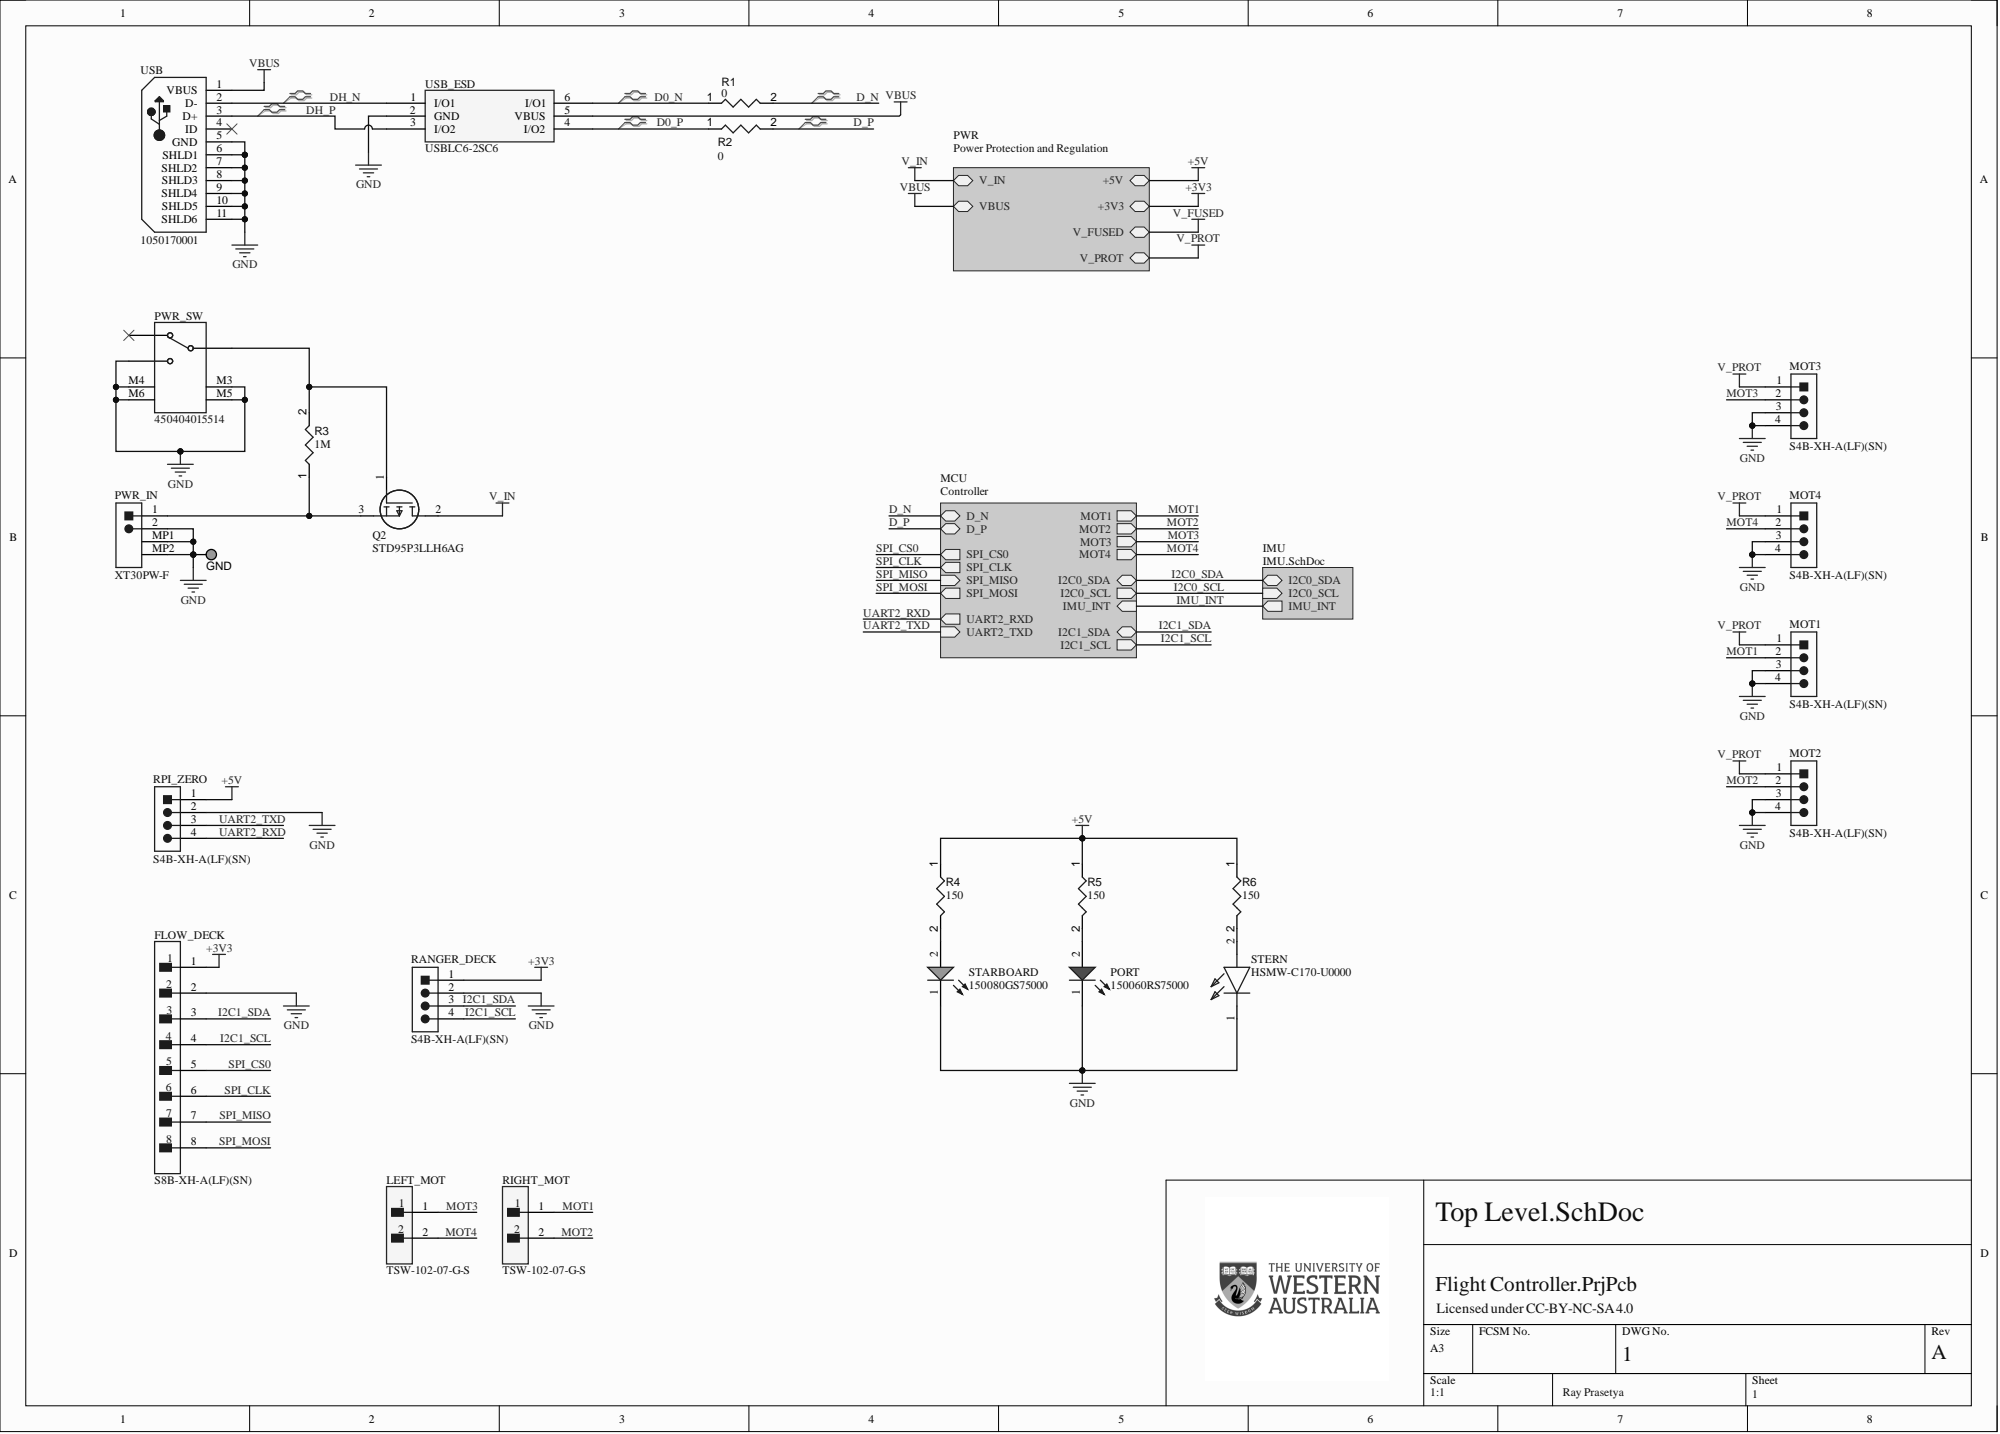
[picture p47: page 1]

PWR
Power Protection and Regulation

Licensed under CC-BY-NC-SA4.0

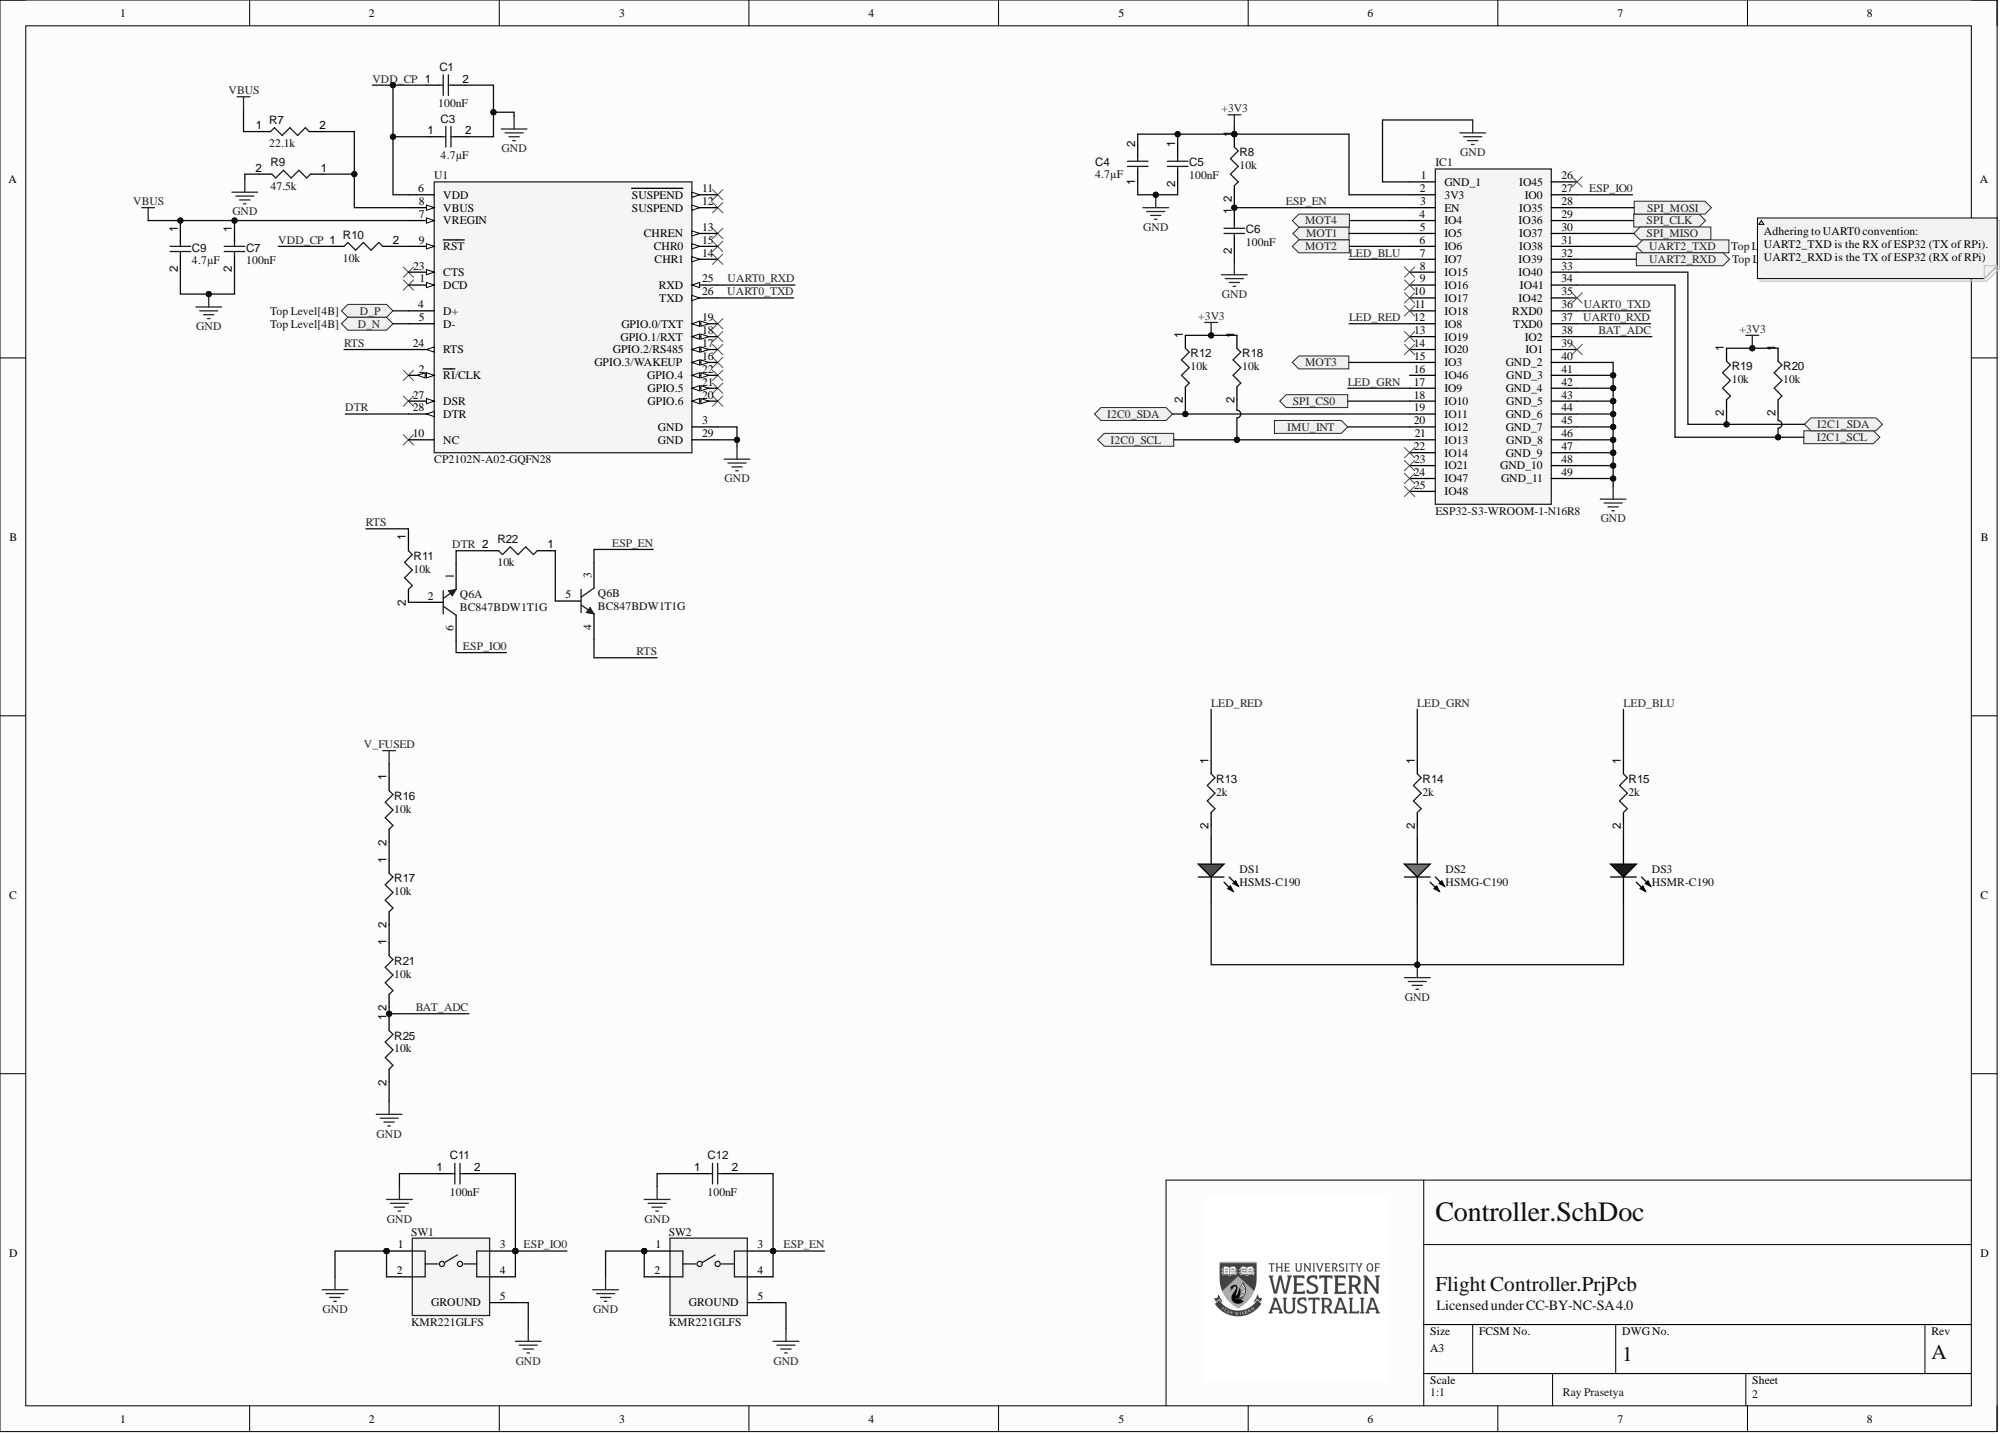
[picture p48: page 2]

Adhering to UART0 convention:
UART2_TXD is the RX of ESP32 (TX of RPi).
UART2_RXD is the TX of ESP32 (RX of RPi)

Flight Controller.PrjPcb
Licensed under CC-BY-NC-SA4.0

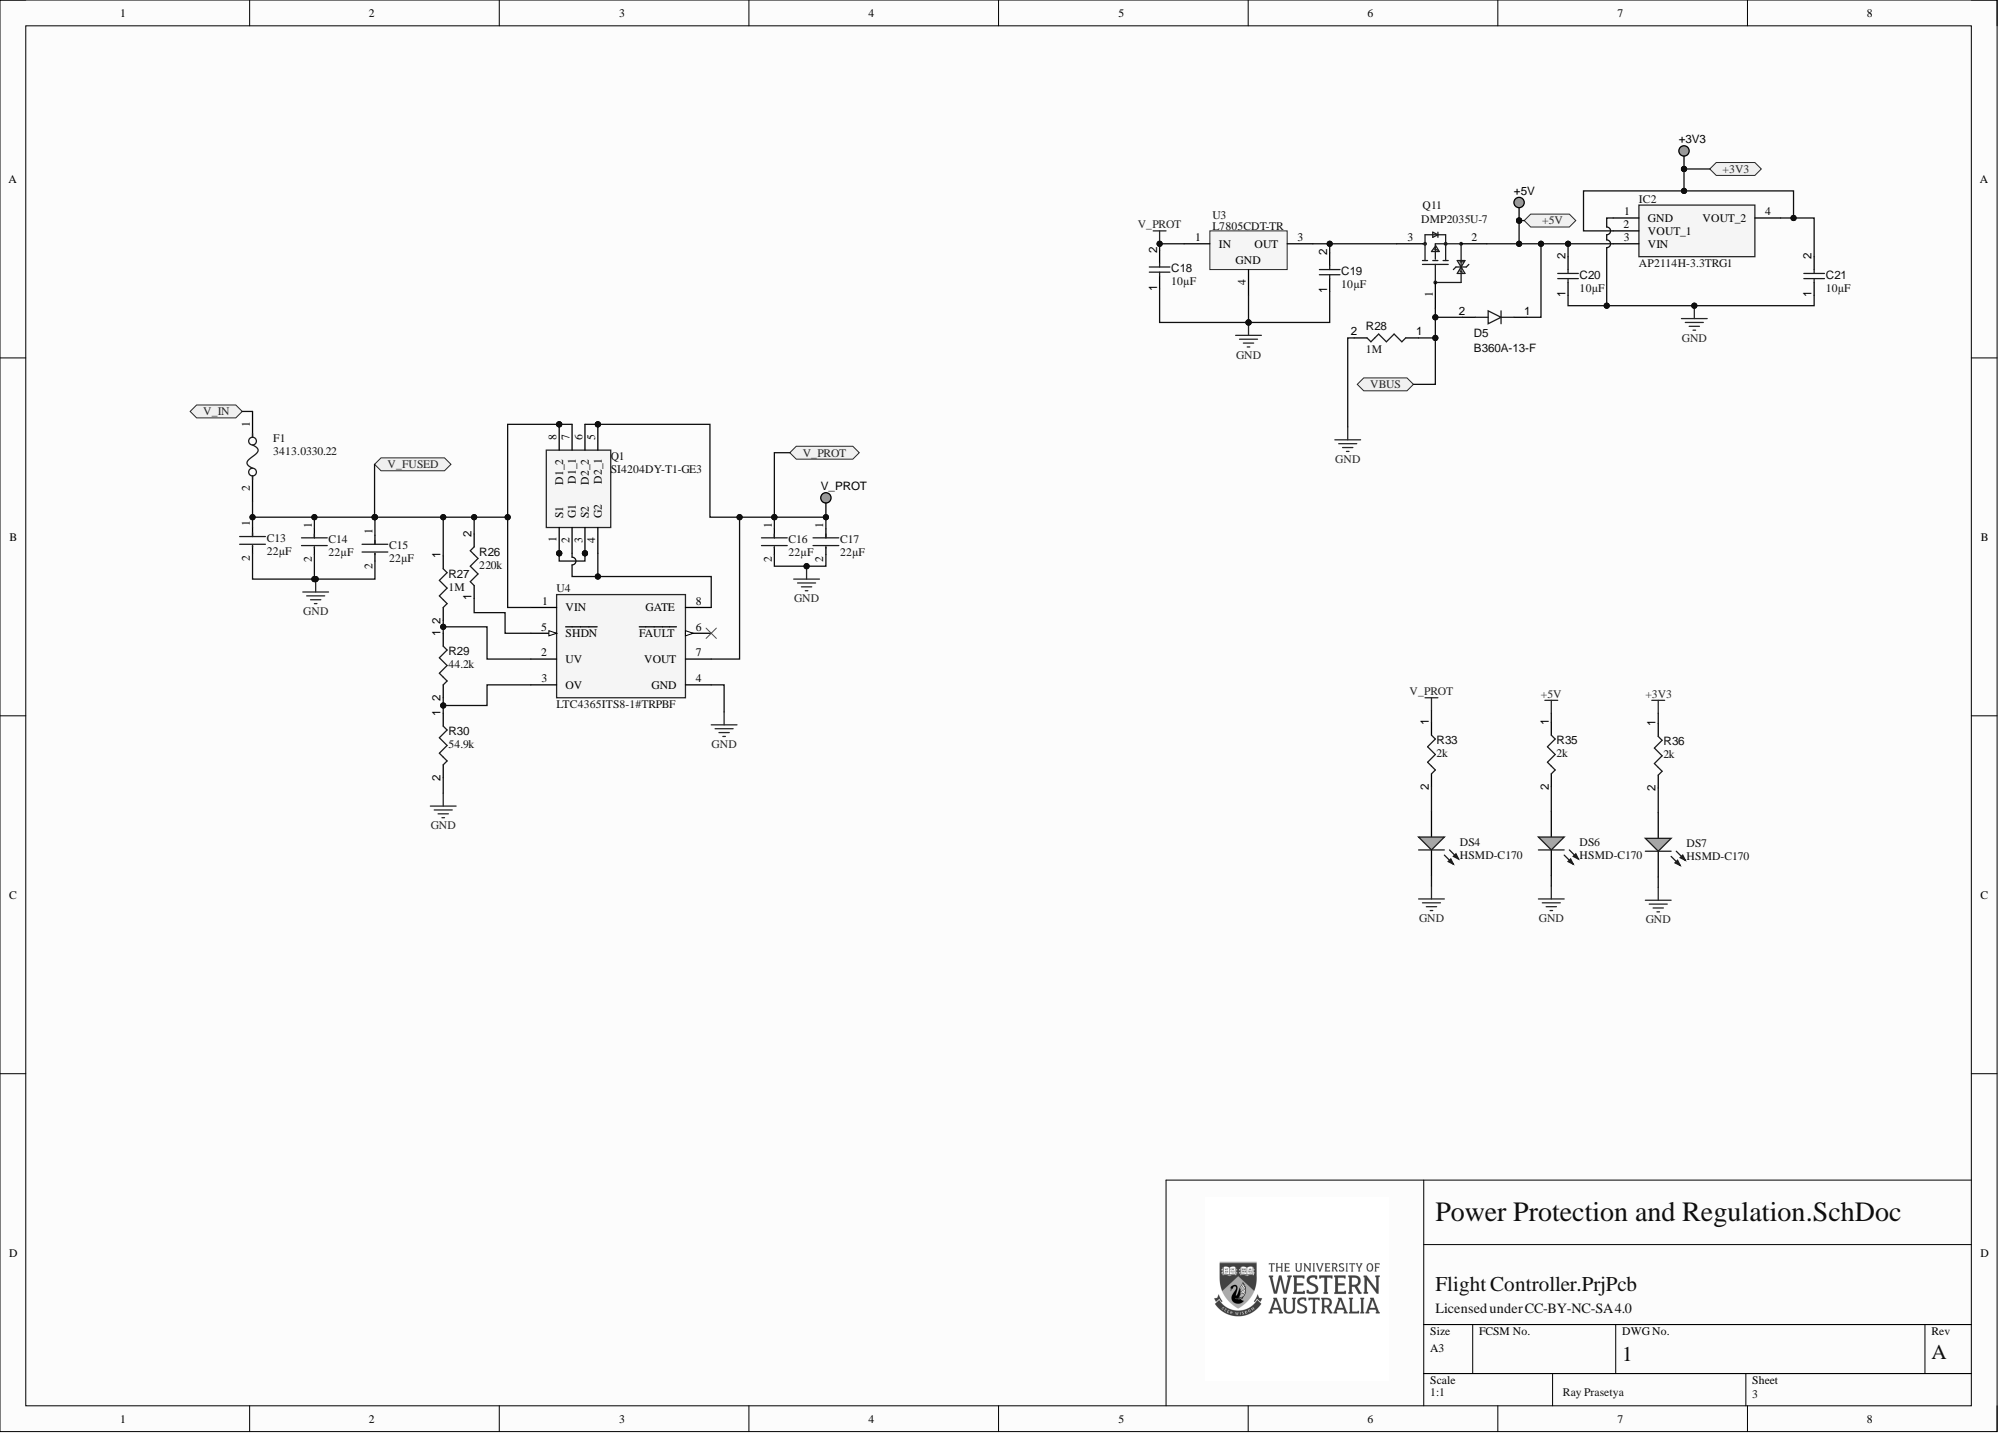
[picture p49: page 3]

5 | FA U LT V O U T G N D | 6 SHDN

Power Protection and Regulation.SchDoc

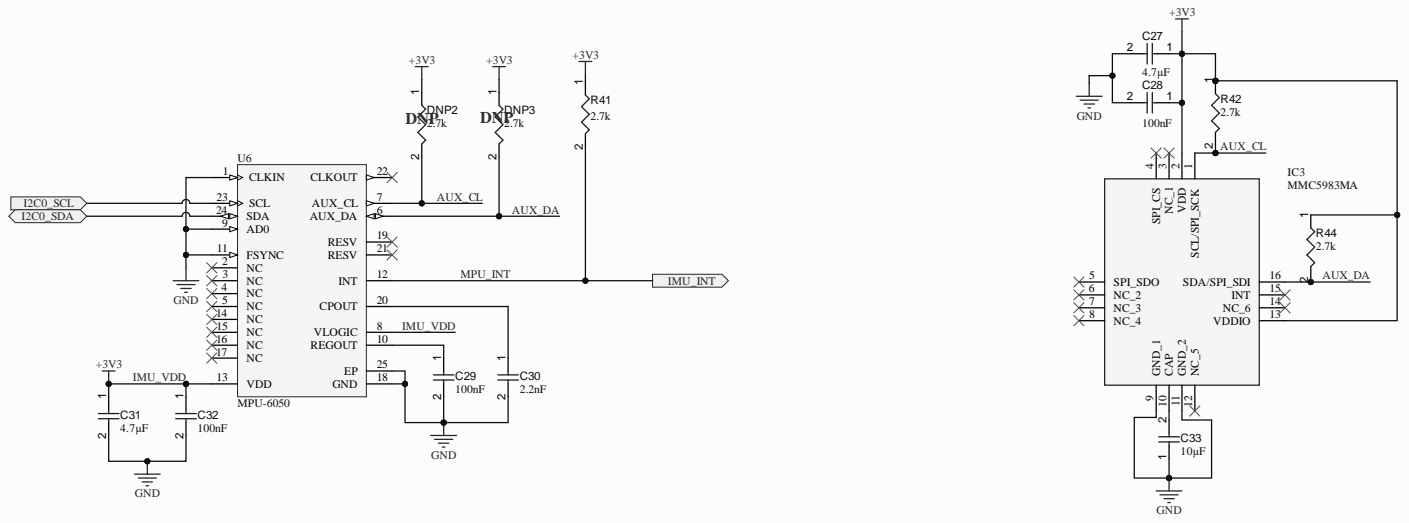
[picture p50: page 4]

1 1
2 | | 2 0

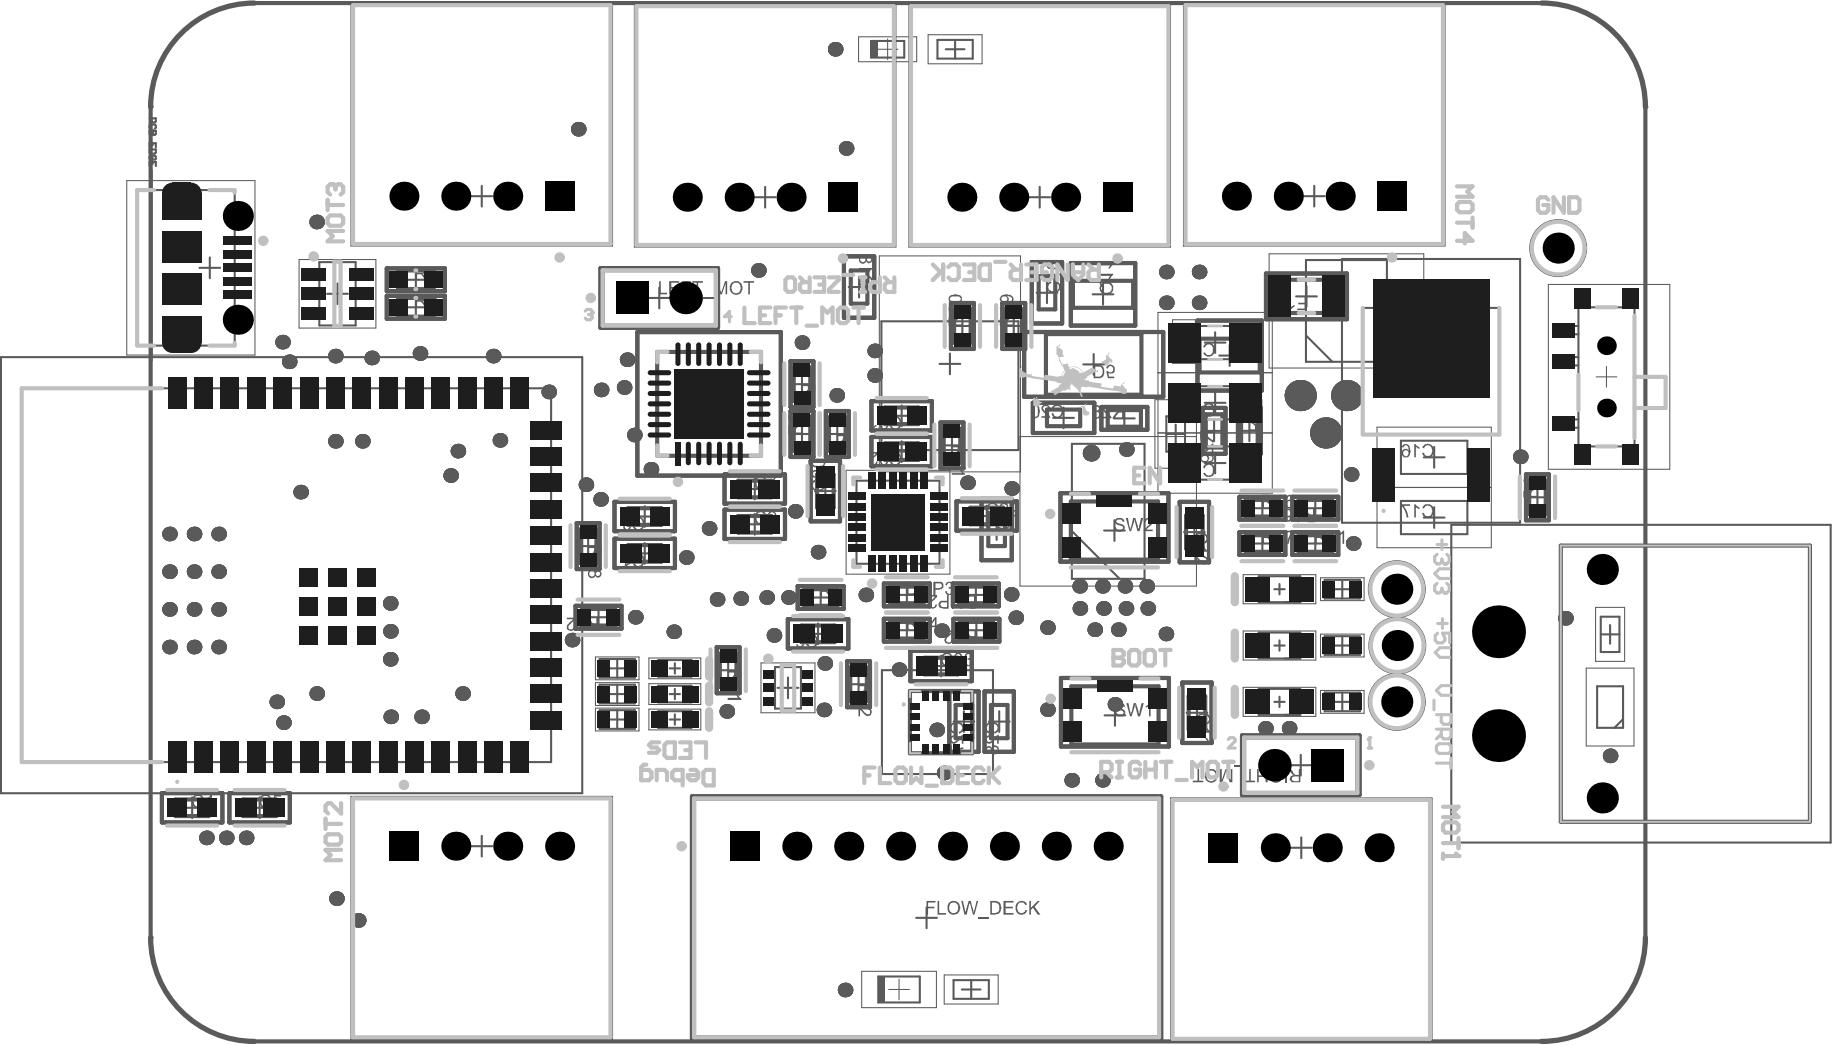
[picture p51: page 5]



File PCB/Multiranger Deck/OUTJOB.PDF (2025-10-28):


GND2 4

GND3 6

Licensed under CC-BY-NC-SA4.0








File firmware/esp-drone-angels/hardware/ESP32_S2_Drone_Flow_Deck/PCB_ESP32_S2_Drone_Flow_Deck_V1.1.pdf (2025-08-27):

# 1C10¹C¹⁰x1 1C¹⁰x2

# 1C71C⁷x1 1C⁷x2

2C4²C⁴x1 2C⁴x2; 1C11C¹x2; 1C¹x1; 1C11 1C¹¹x1; 1C¹¹x2; 1C21C²x2; 1C²x1; 1C31C³x2; 1C³x1; 1C41C⁴x2; 1C⁴x1; 1C51C⁵x2; 1C⁵x1; 1C61C⁶x2; 1C⁶x1; 1C81C⁸x1; 1C⁸x2; 1C91C⁹x1; 1C⁹x2; 1R11R¹x1; 1R¹x2; 1R21R²x2; 1R²x1; 1R31R³x2; 1R³x1; 1R41R⁴x2; 1R⁴x1; 1R51R⁵x1 1R⁵x2; 1U1 ¹U¹x1 1U¹x2 1U¹x3 1U¹x4 1U¹x5 1U¹x6 1U¹x7; 1U¹x8; 1U¹x9; 1U¹x10; 1U¹x11; 1U¹x12; 1U¹x13; 1U¹x14; 1U2 ¹U²x3; 1U²x2; 1U²x1 1U²x4; 1U²x5; 1U3¹U³x1 1U³x2 1U³x3 1U³x4 1U³x7; 1U³x6; 1U³x5 1U³x8 1U³x9 ¹U³x10 1U³x11; 1U³x12; 2C12C¹x2; 2C¹x1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

1J11J1x1 1J1x2 | 1J1x3 1J1x4 | 1J1x5 1J1x6 | 1J1x7 1J1x8 1J1x9 1J1x10 1J1x11 1J1x12 1J1x13 1J1x14 1J1x15

# 1J21J2x1


# #32336 Shield1

200724

#32336 Shield2 200724; Optical Flow; ToF; eCompass; Barometric; Front; 2C5 2C4²C⁴x1 2C⁴x2; 1C11C¹x2; 1C¹x1; 1C10¹C¹⁰x1 1C¹⁰x2; 1C11 1C¹¹x1; 1C¹¹x2; 1C21C²x2; 1C²x1; 1C31C³x2; 1C³x1; 1C41C⁴x2; 1C⁴x1; 1C51C⁵x2; 1C⁵x1; 1C61C⁶x2; 1C⁶x1; 1C71C⁷x1; 1C⁷x2; 1C81C⁸x1; 1C⁸x2; 1C91C⁹x1; 1C⁹x2; 1R11R¹x1; 1R¹x2; 1R21R²x2; 1R²x1; 1R31R³x2; 1R³x1; 1R41R⁴x2; 1R⁴x1; 1R51R⁵x1 1R⁵x2; 1U1 ¹U¹x1 1U¹x2 1U¹x3 1U¹x4 1U¹x5 1U¹x6 1U¹x7; 1U¹x8; 1U¹x9; 1U¹x10; 1U¹x11; 1U¹x12; 1U¹x13; 1U¹x14; 1U2 ¹U²x3; 1U²x2; 1U²x1 1U²x4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

# 1J1¹J1x9 1J1x10 1J1x11 1J1x12 1J1x13 1J1x14 1J1x15

1J2


# #32336 Shield1

200724

#32336 Shield2 200724; Optical Flow; ToF; eCompass; Barometric; Front; 2C4²C⁴x1 2C⁴x2; 1C11C¹x2; 1C¹x1; 1C10¹C¹⁰x1 1C¹⁰x2; 1C11 1C¹¹x1; 1C¹¹x2; 1C21C²x2; 1C²x1; 1C31C³x2; 1C³x1; 1C41C⁴x2; 1C⁴x1; 1C51C⁵x2; 1C⁵x1; 1C61C⁶x2; 1C⁶x1; 1C71C⁷x1; 1C⁷x2; 1C81C⁸x1; 1C⁸x2; 1C91C⁹x1; 1C⁹x2; 1R11R¹x1; 1R¹x2; 1R21R²x2; 1R²x1; 1R31R³x2; 1R³x1; 1R41R⁴x2; 1R⁴x1; 1R51R⁵x1 1R⁵x2; 1U1 ¹U¹x1 1U¹x2 1U¹x3 1U¹x4 1U¹x5 1U¹x6 1U¹x7; 1U¹x8; 1U¹x9; 1U¹x10; 1U¹x11; 1U¹x12; 1U¹x13; 1U¹x14; 1U2 ¹U²x3; 1U²x2; 1U²x1 1U²x4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

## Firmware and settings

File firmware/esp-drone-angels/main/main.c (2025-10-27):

/*
 * ESP-Drone Firmware
 * 
 * Copyright 2019-2020  Espressif Systems (Shanghai) 
 * Copyright (C) 2011-2012 Bitcraze AB
 *
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
 *  Modifications
 *    Copyright (C) Nathan Mayhew 2025
 *      - systemSetMotorsLow
 */

#include <stdint.h>
#include <stdio.h>
#include <stdlib.h>

#include "freertos/FreeRTOS.h"
#include "freertos/task.h"
#include "freertos/portmacro.h"
#include "nvs_flash.h"

#include "stm32_legacy.h"
#include "platform.h"
#include "system.h"
#define DEBUG_MODULE "APP_MAIN"
#include "debug_cf.h"

void app_main()
{
    /*
    * Initialize the platform and Launch the system task
    * app_main will initialize and start everything
    */

    systemSetMotorsLow(); // @@ BLHELI DRIVER

    /* initialize nvs flash prepare for Wi-Fi */
    esp_err_t ret = nvs_flash_init();

    if (ret == ESP_ERR_NVS_NO_FREE_PAGES || ret == ESP_ERR_NVS_NEW_VERSION_FOUND) {
        ESP_ERROR_CHECK(nvs_flash_erase());
        ret = nvs_flash_init();
    }

    ESP_ERROR_CHECK(ret);

    /*Initialize the platform.*/
    if (platformInit() == false) {
        while (1);//if  firmware is running on the wrong hardware, Halt
    }

    /*launch the system task */
    systemLaunch();

}

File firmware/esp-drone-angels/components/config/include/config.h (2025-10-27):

/**
 *
 * ESP-Drone Firmware
 * 
 * Copyright 2019-2020  Espressif Systems (Shanghai) 
 * Copyright (C) 2011-2012 Bitcraze AB
 *
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
 * config.h - Main configuration file
 *
 * This file define the default configuration of the copter
 * It contains two types of parameters:
 * - The global parameters are globally defined and independent of any
 *   compilation profile. An example of such define could be some pinout.
 * - The profiled defines, they are parameter that can be specific to each
 *   dev build. The vanilla build is intended to be a "customer" build without
 *   fancy spinning debugging stuff. The developers build are anything the
 *   developer could need to debug and run his code/crazy stuff.
 *
 * The golden rule for the profile is NEVER BREAK ANOTHER PROFILE. When adding a
 * new parameter, one shall take care to modified everything necessary to
 * preserve the behavior of the other profiles.
 *
 * For the flag. T_ means task. H_ means HAL module. U_ would means utils.
 * 
 * Modifications
 *  Copyright (C) Nathan Mayhew 2025
 *    - Multiranger task
 */

#ifndef CONFIG_H_
#define CONFIG_H_
//#include "nrf24l01.h"

//#include "trace.h"
#include "usec_time.h"
#include "sdkconfig.h"

#define PROTOCOL_VERSION 4
#define QUAD_FORMATION_X

#ifdef CONFIG_TARGET_ESPLANE_V2_S2
#ifndef CONFIG_IDF_TARGET_ESP32S2
#error "ESPLANE_V2 hardware with ESP32S2 onboard"
#endif
#elif defined(CONFIG_TARGET_ESPLANE_V1)
#ifndef CONFIG_IDF_TARGET_ESP32
#error "ESPLANE_V1 hardware with ESP32 onboard"
#endif
#elif defined(CONFIG_TARGET_ESP32_S2_DRONE_V1_2)
#ifdef CONFIG_IDF_TARGET_ESP32
#error "ESP32_S2_DRONE_V1_2 hardware with ESP32S2/S3 onboard"
#endif
#endif

#ifdef STM32F4XX 
  #define CONFIG_BLOCK_ADDRESS    (2048 * (64-1))
  #define MCU_ID_ADDRESS          0x1FFF7A10
  #define MCU_FLASH_SIZE_ADDRESS  0x1FFF7A22
  #ifndef FREERTOS_HEAP_SIZE
    #define FREERTOS_HEAP_SIZE      20000
  #endif
  #define FREERTOS_MIN_STACK_SIZE 150       // M4-FPU register setup is bigger so stack needs to be bigger
  #define FREERTOS_MCU_CLOCK_HZ   168000000

  #define configGENERATE_RUN_TIME_STATS 1
  #define portCONFIGURE_TIMER_FOR_RUN_TIME_STATS() initUsecTimer()
  #define portGET_RUN_TIME_COUNTER_VALUE() usecTimestamp()
#endif


//#define DEBUG_UDP
//#define DEBUG_EP2

// Task priorities. Higher number higher priority
// system state tasks
#define SYSTEM_TASK_PRI         1
#define PM_TASK_PRI             1
#define LEDSEQCMD_TASK_PRI      1
// communication TX tasks
#define UDP_TX_TASK_PRI         2
#define CRTP_TX_TASK_PRI        2
#define IMU_UART_TASK_PRI       5   // EDIT
#define UART_SYNC_TASK_PRI      9   // EDIT
// communication RX tasks
#define UDP_RX_TASK_PRI         2
#define EXTRX_TASK_PRI          2
#define UART2_TASK_PRI          2
#define SYSLINK_TASK_PRI        2
#define USBLINK_TASK_PRI        2
#define WIFILINK_TASK_PRI       2
#define CRTP_RX_TASK_PRI        2
#define CMD_HIGH_LEVEL_TASK_PRI 3
#define INFO_TASK_PRI           2
#define LOG_TASK_PRI            2
#define MEM_TASK_PRI            2
#define PARAM_TASK_PRI          2
// sensors and stabilize related tasks
#define PROXIMITY_TASK_PRI      5
#define FLOW_TASK_PRI           5
#define ZRANGER2_TASK_PRI       5
#define ZRANGER_TASK_PRI        5
#define SENSORS_TASK_PRI        6
#define STABILIZER_TASK_PRI     7
#define KALMAN_TASK_PRI         4
#define MULTIRANGER_TASK_PRI    4 // @@ Added Stack overflow at 5

// the kalman filter consumes a lot of CPU
// for single core systems, we need to lower the priority
#if CONFIG_FREERTOS_UNICORE
  #undef KALMAN_TASK_PRI
  #define KALMAN_TASK_PRI         1
#endif

// Task names
#define CMD_HIGH_LEVEL_TASK_NAME "CMDHL"
#define CRTP_RX_TASK_NAME       "CRTP-RX"
#define CRTP_TX_TASK_NAME       "CRTP-TX"
#define EXTRX_TASK_NAME         "EXTRX"
#define FLOW_TASK_NAME          "FLOW"
#define IMU_UART_TASK_NAME      "IMU_UART"    // EDIT
#define KALMAN_TASK_NAME        "KALMAN"
#define LEDSEQCMD_TASK_NAME     "LEDSEQCMD"
#define LOG_TASK_NAME           "LOG"
#define MEM_TASK_NAME           "MEM"
#define PARAM_TASK_NAME         "PARAM"
#define PM_TASK_NAME            "PWRMGNT"
#define PROXIMITY_TASK_NAME     "PROXIMITY"
#define SENSORS_TASK_NAME       "SENSORS"
#define STABILIZER_TASK_NAME    "STABILIZER"
#define SYSLINK_TASK_NAME       "SYSLINK"
#define SYSTEM_TASK_NAME        "SYSTEM"
#define UART2_TASK_NAME         "UART2"
#define UART_SYNC_TASK_NAME     "UART_SYNC"   // EDIT
#define UDP_RX_TASK_NAME        "UDP_RX"
#define UDP_TX_TASK_NAME        "UDP_TX"
#define USBLINK_TASK_NAME       "USBLINK"
#define WIFILINK_TASK_NAME      "WIFILINK"
#define ZRANGER2_TASK_NAME      "ZRANGER2"
#define ZRANGER_TASK_NAME       "ZRANGER"
#define MULTIRANGER_TASK_NAME   "MULTIRANGER" // @@ Added
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

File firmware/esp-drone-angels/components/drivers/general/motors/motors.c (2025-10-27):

/**
 *
 * ESP-Drone Firmware
 *
 * Copyright 2019-2020  Espressif Systems (Shanghai)
 * Copyright (C) 2011-2012 Bitcraze AB
 *
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
 * motors.c - Motor driver
 *
 * Modifications
 *  Copyright (C) Nathan Mayhew 2025
 *      - Thrust map limiting
 *      - 1-2ms PWM signal mapping
 */

#include <stdbool.h>

//FreeRTOS includes
#include "freertos/FreeRTOS.h"
#include "freertos/task.h"

#include "stm32_legacy.h"
#include "motors.h"
#include "pm_esplane.h"
#include "log.h"
#define DEBUG_MODULE "MOTORS"
#include "debug_cf.h"

#define THRUSTMAP_MAX 50000u//41000u // @@ max thrust to remap to (0-65536)
// @@ you should update the kalman filter CONTROL_TO_ACC macro in 'estimator_kalman.c' when adjusting thrust limits
// @@ but obviously you need to know the corresponding max thrust to do properly
// @@ the line to change is: #define CONTROL_TO_ACC (GRAVITY_MAGNITUDE*300.0f/(CF_MASS*1000.0f)/41000.0f)
// @@                                                              grams ^           THRUSTMAP_MAX ^

static uint16_t motorsConvBitsTo16(uint16_t bits);
static uint16_t motorsConv16ToBits(uint16_t bits);
static uint16_t motorsThrustMap(uint16_t bits); // @@
static uint16_t motorsThrustInverseMap(uint16_t bits); // @@



uint32_t motor_ratios[] = {0, 0, 0, 0};

void motorsPlayTone(uint16_t frequency, uint16_t duration_msec);
void motorsPlayMelody(uint16_t *notes);
void motorsBeep(int id, bool enable, uint16_t frequency, uint16_t ratio);

const MotorPerifDef **motorMap; /* Current map configuration */

const uint32_t MOTORS[] = {MOTOR_M1, MOTOR_M2, MOTOR_M3, MOTOR_M4};

const uint16_t testsound[NBR_OF_MOTORS] = {A4, A5, F5, D5};

static bool isInit = false;
static bool isTimerInit = false;

ledc_channel_config_t motors_channel[NBR_OF_MOTORS] = {
    {
        .channel = MOT_PWM_CH1,
        .duty = 0, // @@ TODO: Maybe this could be set to the half resolution instead of the initialisation GPIO method? 
        .gpio_num = MOTOR1_GPIO,
        .speed_mode = LEDC_LOW_SPEED_MODE,
        .timer_sel = LEDC_TIMER_0
    },
    {
        .channel = MOT_PWM_CH2,
        .duty = 0,
        .gpio_num = MOTOR2_GPIO,
        .speed_mode = LEDC_LOW_SPEED_MODE,
        .timer_sel = LEDC_TIMER_0
    },
    {
        .channel = MOT_PWM_CH3,
        .duty = 0,
        .gpio_num = MOTOR3_GPIO,
        .speed_mode = LEDC_LOW_SPEED_MODE,
        .timer_sel = LEDC_TIMER_0
    },
    {
        .channel = MOT_PWM_CH4,
        .duty = 0,
        .gpio_num = MOTOR4_GPIO,
        .speed_mode = LEDC_LOW_SPEED_MODE,
        .timer_sel = LEDC_TIMER_0
    },
};
/* Private functions */

// @@ This function is used for estimation and logging
static uint16_t motorsConvBitsTo16(uint16_t bits)
{
    bits = motorsThrustInverseMap(bits); // @@

    // @@ This function has been modified to map 128-256 (8 bit) to 0-65535 (16 bit)
    // return ((bits) << (16 - MOTORS_PWM_BITS)); // original crazyflie line
    return (bits - (1 << (MOTORS_PWM_BITS-1))) << (16 - MOTORS_PWM_BITS + 1); // @@ 
}   

// @@ This function is for mapping the Thrust command (16 bit) to a Duty Cycle (8 bit, only 128-256)
static uint16_t motorsConv16ToBits(uint16_t bits)
{
    bits = motorsThrustMap(bits); // @@

    // @@ This function has been modified to map 0-65535 (16 bit) to 128-256 (8 bit) for MOTORS_PWM_BITS=8 (will work for any MOTORS_PWM_BITS <= 17)
    // return ((bits) >> (16 - MOTORS_PWM_BITS) & ((1 << MOTORS_PWM_BITS) - 1)); // original crazyflie line
    return (bits >> (16 - MOTORS_PWM_BITS + 1)) + (1 << (MOTORS_PWM_BITS-1)); // @@ explanation: bitshift down 9 bits (maps to 0-127), then add 128 (maps to 127-255) 
}

// @@ Custom Function - Linearly remap the thrust to limit power
// @@ ie.     T ---->[THRUST Map]---T'---->[motorsConv16ToBits]----DutyCycle--->Motors
// @@ where T = Thrust Input (0-65535); T' = Mapped Thrust (0-THRUSTMAP_MAX); DutyCycle = 128-256 (but upper range of DutyCycle is limited by THRUSTMAP_MAX)
// @@ (although this function is technically a part of motorsConv16ToBits so only motorsConv16ToBits needs to be called)
static uint16_t motorsThrustMap(uint16_t bits)
{   
    uint32_t mappedThrust = ((uint32_t)bits * THRUSTMAP_MAX) / 65535u;

    return (uint16_t)mappedThrust;
}


// @@ Custom Function - Do the inverse of the limit mapping so that 100% Thrust is still 65535 outside of the motor driver.
static uint16_t motorsThrustInverseMap(uint16_t bits)
{
    uint32_t demappedThrust =  ((uint32_t)bits * 65535u) / THRUSTMAP_MAX;

    return (uint16_t)demappedThrust;
}

bool pwm_timmer_init()
{
    if (isTimerInit) {
        // First to init will configure it
        return TRUE;
    }

    /*
     * Prepare and set configuration of timers
     * that will be used by MOTORS Controller
     */
    ledc_timer_config_t ledc_timer = {
        .duty_resolution = MOTORS_PWM_BITS, // resolution of PWM duty
        .freq_hz = 500,					// frequency of PWM signal @@ MODIFICATION (originally 15000Hz)
        .speed_mode = LEDC_LOW_SPEED_MODE, // timer mode
        .timer_num = LEDC_TIMER_0,			// timer index
        // .clk_cfg = LEDC_AUTO_CLK,              // Auto select the source clock
    };

    // Set configuration of timer0 for high speed channels
    if (ledc_timer_config(&ledc_timer) == ESP_OK) {
        isTimerInit = TRUE;
        return TRUE;
    }

    return FALSE;
}

/* Public functions */

//Initialization. Will set all motors ratio to 0% //@@ Probably not good thing?
void motorsInit(const MotorPerifDef **motorMapSelect)
{
    int i;

    if (isInit) {
        // First to init will configure it
        return;
    }

    motorMap = motorMapSelect;

    if (pwm_timmer_init() != TRUE) {
        return;
    }

    for (i = 0; i < NBR_OF_MOTORS; i++) {
        ledc_channel_config(&motors_channel[i]);
    }

    isInit = true;
}

void motorsDeInit(const MotorPerifDef **motorMapSelect)
{
    for (int i = 0; i < NBR_OF_MOTORS; i++) {
        ledc_stop(motors_channel[i].speed_mode, motors_channel[i].channel, 0);
    }
}

bool motorsTest(void)
{
    int i;

    for (i = 0; i < sizeof(MOTORS) / sizeof(*MOTORS); i++) {
        if (motorMap[i]->drvType == BRUSHED) {
#ifdef ACTIVATE_STARTUP_SOUND
            motorsBeep(MOTORS[i], true, testsound[i], (uint16_t)(MOTORS_TIM_BEEP_CLK_FREQ / A4) / 20);
            vTaskDelay(M2T(MOTORS_TEST_ON_TIME_MS));
            motorsBeep(MOTORS[i], false, 0, 0);
            vTaskDelay(M2T(MOTORS_TEST_DELAY_TIME_MS));
#else
            motorsSetRatio(MOTORS[i], MOTORS_TEST_RATIO);
            vTaskDelay(M2T(MOTORS_TEST_ON_TIME_MS));
            motorsSetRatio(MOTORS[i], 0);
            vTaskDelay(M2T(MOTORS_TEST_DELAY_TIME_MS));
#endif
        }
    }

    return isInit;
}

// Ithrust is thrust mapped for 65536 <==> 60 grams
// @@ So ithrust is 16 bits
void motorsSetRatio(uint32_t id, uint16_t ithrust)
{
    if (isInit) {
        uint16_t ratio;

        ASSERT(id < NBR_OF_MOTORS);

        ratio = ithrust;
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

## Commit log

2025-08-27 Removed the top-level ESPDrone and CFClient folders; Created Firmware folder with a main folder (for the main build of the project) and a testing folder (for unit-testing modifications to the firmwar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
    [BOM(0.2)_ESP32-S2-Drone_V1.2_20200512.xlsx, BOM_200616.xlsx, SCH_ESP32_S2_Drone_Flow_Deck_V1.1.DSN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]
2025-08-28 Added BLHeli ESC PWM test control script in firmware testing
2025-08-28 Updated modification register with some motors items and changed ESC Testing README
2025-08-29 Modified BLHeli Driver to produce 1ms-2ms pulses at 500Hz
    [BOM(0.2)_ESP32-S2-Drone_V1.2_20200512.xlsx, BOM_200616.xlsx, SCH_ESP32_S2_Drone_Flow_Deck_V1.1.DSN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]
2025-08-30 Added 'BLHeli Driver' folder in testing, which integrates the BLHeli ESC into the Crazyflie firmware.
    [BOM(0.2)_ESP32-S2-Drone_V1.2_20200512.xlsx, BOM_200616.xlsx, SCH_ESP32_S2_Drone_Flow_Deck_V1.1.DSN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]
2025-09-02 Erwin finishing Pi notes + Makefile
    Completed documenting my Pi setup process, added a project Makefile to automate streaming on the groundstation.
2025-09-07 VL53L1 Testing files added
    [BOM(0.2)_ESP32-S2-Drone_V1.2_20200512.xlsx, BOM_200616.xlsx, SCH_ESP32_S2_Drone_Flow_Deck_V1.1.DSN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]
2025-09-18 BLHeli Driver initialisation, VLHeli Battery Management, Multiranger script, CFlib reverse engineering
    [BOM(0.2)_ESP32-S2-Drone_V1.2_20200512.xlsx, BOM_200616.xlsx, SCH_ESP32_S2_Drone_Flow_Deck_V1.1.DSN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]
2025-09-27 ULD API for Multiranger
    [BOM(0.2)_ESP32-S2-Drone_V1.2_20200512.xlsx, BOM_200616.xlsx, LIDAR_VL53L1X_Ultra_Lite_Driver Debug.cfg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]
2025-10-08 UART stuff
2025-10-11 God knows (nav scripting, main integration, deadcat motor mixing, power management SOC table)
    [BOM(0.2)_ESP32-S2-Drone_V1.2_20200512.xlsx, BOM_200616.xlsx, SCH_ESP32_S2_Drone_Flow_Deck_V1.1.DSN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]
2025-10-13 Adjusted thrust limits and testing files
    [BOM(0.2)_ESP32-S2-Drone_V1.2_20200512.xlsx, BOM_200616.xlsx, SCH_ESP32_S2_Drone_Flow_Deck_V1.1.DSN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]
2025-10-13 Erwin's Notes, UDP, and UART stuff
2025-10-27 added orbslam workspace from ground station
2025-10-27 added cf-ros2-nav workspace
    [1.csv, 10.csv, 11.csv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]
2025-10-27 Updated README. TODO: Add LICENSE.TXT
    [BOM(0.2)_ESP32-S2-Drone_V1.2_20200512.xlsx, BOM_200616.xlsx, LIDAR_VL53L1X_Ultra_Lite_Driver Debug.cfg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]
2025-10-27 uart fixes
2025-10-27 technically a merge plus restructure
    [BOM(0.2)_ESP32-S2-Drone_V1.2_20200512.xlsx, BOM_200616.xlsx, SCH_ESP32_S2_Drone_Flow_Deck_V1.1.DSN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]
2025-10-27 monikas frame files
    [Big_leg_V2_light.step, Bottom_Plate_V5_light.step, Frnt_Guard_V6_filround.step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]
2025-10-28 updated README, updated PCB files, added user manual
    [Bill of Materials-Flight Controller.xlsx, Bill of Materials-FlowdeckPCB1.xlsx, Daughter-ToFDaughters_breakoff_small.xlsx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]

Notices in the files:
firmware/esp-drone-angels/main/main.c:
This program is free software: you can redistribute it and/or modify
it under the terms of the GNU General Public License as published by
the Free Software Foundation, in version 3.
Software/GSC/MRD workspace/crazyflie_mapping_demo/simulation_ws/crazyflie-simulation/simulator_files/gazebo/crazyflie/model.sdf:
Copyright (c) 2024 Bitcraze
